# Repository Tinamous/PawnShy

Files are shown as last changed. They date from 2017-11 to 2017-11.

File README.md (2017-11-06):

# Pawn Shy

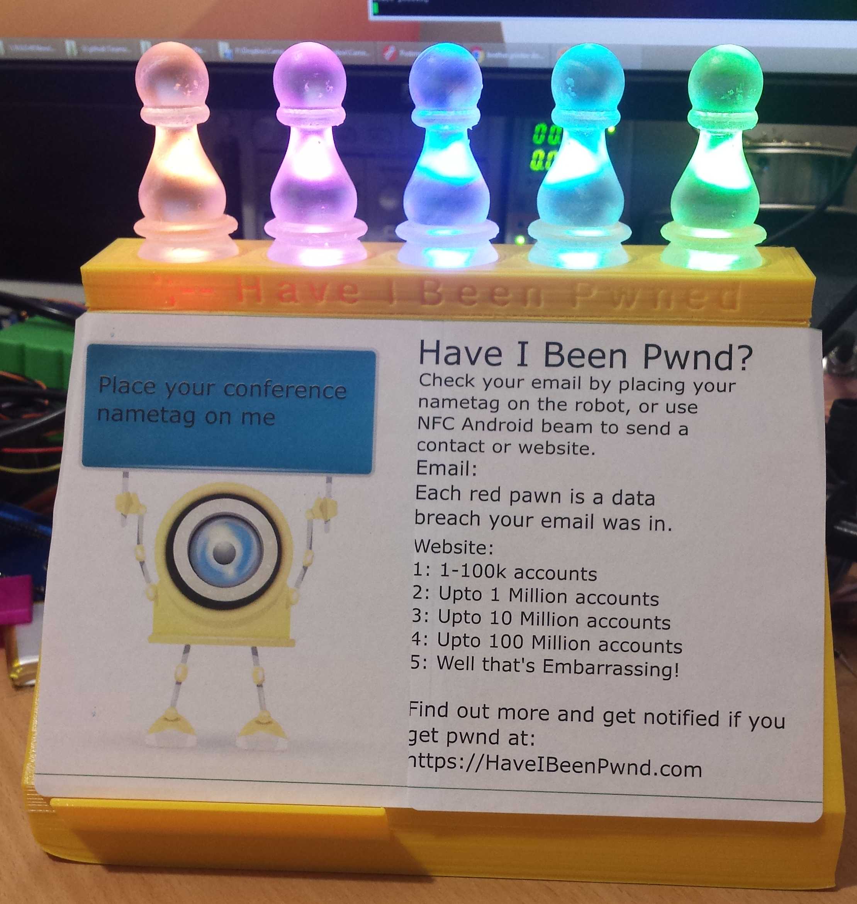
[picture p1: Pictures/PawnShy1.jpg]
Pawn Shy


This is my entry to the Have I Been Pwned API competition.

Based on the fair ground game Coconut shy. The aim is to knock out as many pawns as possible using either your email address or website that hasn't been pwned (good luck with that!).

## Videos:

[Part 1](https://youtu.be/ber4mi4SVx4)

[Part 2](https://youtu.be/kG7oJAG3vGs)

The game is intended to be easy to play, for example, at a conference, and to give the player a fun visual indication, and to drive their interest in Have I Been Pwned.

When attending Signal London recently I noticed the attendee name badges were actually NFC cards, this could be used either to lookup the attendees email (or hash) or have the email/hash directly in the NFC card.

Whilst the Signal NFC cards didn't actually include my email address it would have been easy for Twilio to add a VCard for me, or a hash of my email to facilitate this game.

Likewise, many door entry systems use NFC or RFID cards. These cards could be linked to an email address through an external database and provide a simple and fun way for employees to check if their email has been pwned.

## How It's Made

* Raspberry Pi running Raspbian
* I actually used the OctoPi 0.14 image for this. (It isn't required, but it makes it easy to start the Pi headless and I had other reasons as well)
* NFC sensor (Micro NFC Board - https://www.seeedstudio.com/Micro-NFC-Board-p-2431.html)
* 5 LED Neopixel strip (https://www.adafruit.com/product/1376)
* 3D Printed case
* 3D (SLA) printed pawns

The Raspberry Pi polls the NFC sensor waiting for a card or p2p connection and reads the following to get an email/website:

* Card serial number - linked though an external database to email address
* Uri NDEF record for a website
* VCard NDEF record for email address (Not implemented)
* P2P uri send for a website

Once the Pi picks up an email or website the Have I Been Pwned API is queried to get either:

* the number of times the email appears in a pwned site or 
* the number of accounts compromised for the website.

This is then displayed through the 5 pixel NeoPixel LEDs.

* As 0-5 Red/Purple vs Green/Yellow colouring for the count
* A sliding scale (1-100k, <1M, <10M, <100M, Wooo) of red/purple pwns indicting the number of accounts compromised.

Colours: typically Red for a compromise or Green when not used. However if using Minion pawns then Purple (bad minion) or Yellow (good minion/banana).

The LEDs are placed under the pawns and hidden from sight so it looks like the pawns are glowing.

Optional: A printer could be connected which prints out details of the compromise to allow the user to read up further.

## Games:

### Game 1: Have I Been Pwned

The aim of this game is to use your email address and make all the pawns go green (or yellow for Minion pawns).

Present a NFC card that either includes your email address, a hash or the id is linked to a database or email addresses (e.g. a door key)

Each red (or purple minion) pawn indicates the count of compromised sites the email is associated with.

### Game 2: Have They Been Pwned

The aim of this game is to find the website that has not been pwned, or in multi-player mode, to find the website with the lowest pwnage.

Using pre-programmed NFC cards, select a card for the website you trust the most. Present the the Game Of Pwned sensor.

Each red/purple pwnd indicates a pwnage.
0: Yay, not pwned!
1: 1-100k accounts compromised.
2: <1M
3: <10M
4: <100M
5: OUCH!

For multi-player you each select a card and the winner is the person with the lowest pwnage.

### Game 3: Send in the pwnage (Android Only)

Like game 2, the aim of this game is to find your favorite website without pwnage.

Ensure NFC Android Beam is enabled on your phone.

Browse to a website you trust (or don't!) and have an account with.

Place your phone on the Game Of Pwned.

When promoted by your phone click to send the website.

As with game 2. The pwnd accounts are displayed.

## Construction

### NeoPixels

Neopixels need to be driven with a serial data signal 70% of the power supply, and can work from a 3.6-5V Power supply. Sadly the Pi uses 3v3 for it's signals so the 3v3 power will not power the neopixels so our only choice is to use the 5V power. This then means that the 3v3 DIn will not be within the 70% required value. So we use a small diode inline with the 5V supply to drop it down to 4V4, brining our 3v3 signal to 75% of the power signal. With only 5 LEDs being driven the current draw should be low (300mA max) so a IN4001 diode will be more than sufficient.

* Cut a Neopixel strip to 5 LEDs along the cut line shown on the taps.
* Connect 3 wires to the input (5V/DIn/Gnd) side of the Neopixel strip.
* Connect a IN4001 diode in the 5V line with the current flow going towards the LEDs (diode band nearest the LEDs). Connect the other end of the diode to the 5V Pin.
* Connect a 300-600 Ohm resistor to the Din wire (to limit the current and protect the LEDs). Connect the other end of this to Pin 12 on the Pi).
* Connect Gnd straight to the Pi.

Note that Neopixels are not really a good choice for use on the Raspberry Pi. 

Install the raspberry Pi Neopixel software following the instructions here:

https://learn.adafruit.com/neopixels-on-raspberry-pi/software

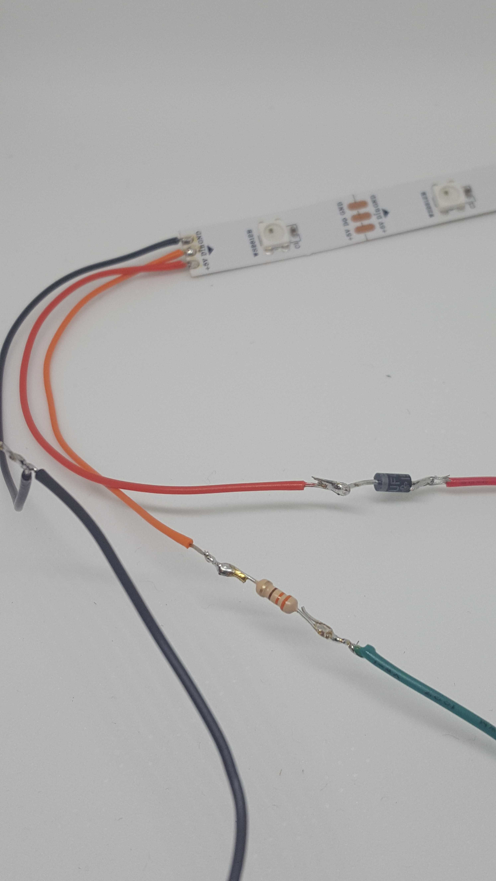
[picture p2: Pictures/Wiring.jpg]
Neopixel Wiring


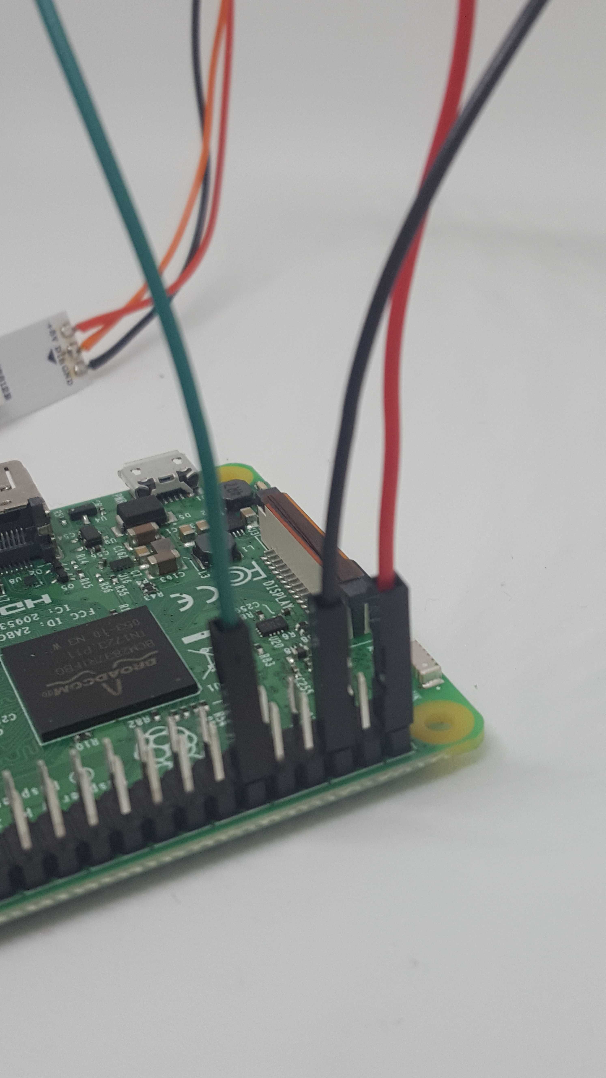
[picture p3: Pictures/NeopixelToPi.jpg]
Neopixel To Pi


## Pi

Ensure Neopixel LEDs connected as:

* Pin 2 = +5V
* Pin 6 = GND
* Pin 12 = DIn

Connect a USB power cable to the Pi before mounting (You might not be able to plug into the Pi once mounted).

Ensure your SD card in the Pi is working.

Mount the pi inside on the back wall. Use four M2.5 x6mm machine screws from the back into M2.5 x 11mm standoffs (Farnell 294583) which the Pi is mounted to, then M2.5 nuts on the other side of the Pi to secure it.

## NFC reader

If you're using M3 heat fit inserts to bold the holder to the case fit these with a hot soldering iron. Ensure that that are facing the correct way (fat end up with the large open area of the holder up as well).

Using a Micro NFC Board place this in the 3D printed holder with the component side of the PCB facing down into the holder so the blank side will sit against the inside of the case.

Fit the USB lead to the NFB board.

Screw the holder to the inside of the case. It doesn't quite fit in the center due to the USB connector, so it's pushed to one side.

Plug the USB lead into the Raspberry Pi.

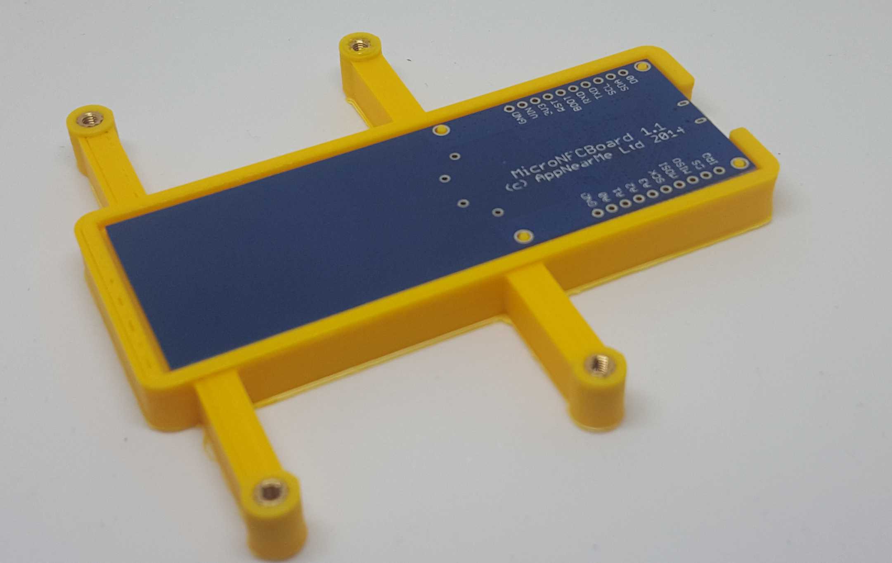
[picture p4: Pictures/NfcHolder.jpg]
NFC Holder


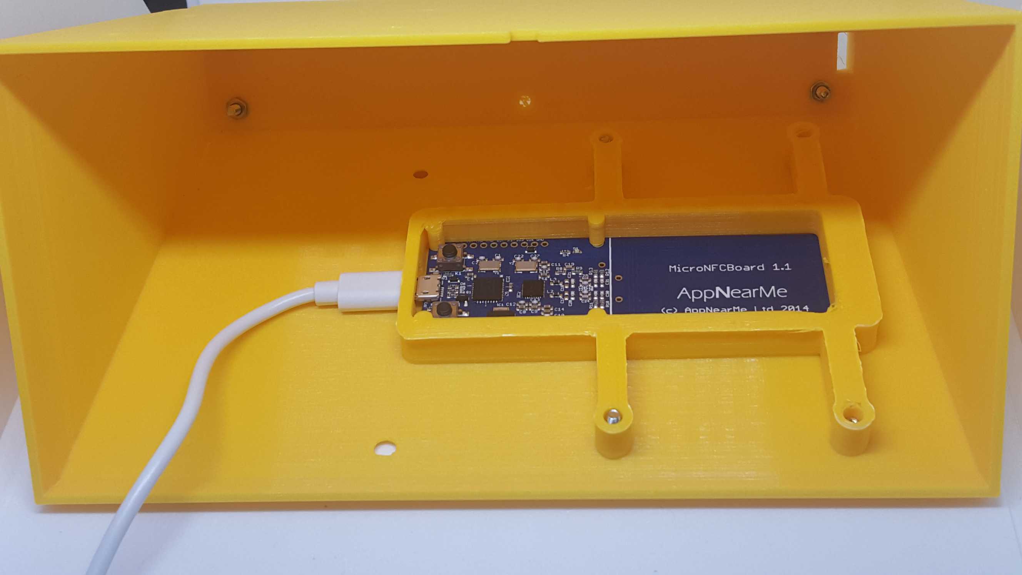
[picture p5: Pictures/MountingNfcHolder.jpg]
Mounting the NFC Holder


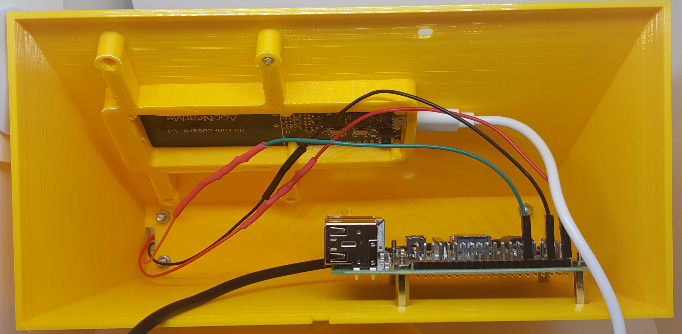
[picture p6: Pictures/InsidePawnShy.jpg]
Inside Pawn Shy


## Pawns:

The pawns are 3D Printed (I used a Form2 with clear resin as this gives a nice print). 

Various Pawn models are available:

* Eureka Pawn: https://www.thingiverse.com/thing:173436
* Bender Bust: https://www.thingiverse.com/thing:182789
* Bender Can Holder: http://www.thingiverse.com/thing:1513101
* Minions: https://www.thingiverse.com/thing:376059

The models should be resized to about 26mm on the x/y axis to fit the stand.

Eureka Pawn and Bender are also available in the Pawns folder as hollowed out versions which might work better for FDM printers with clear filament.

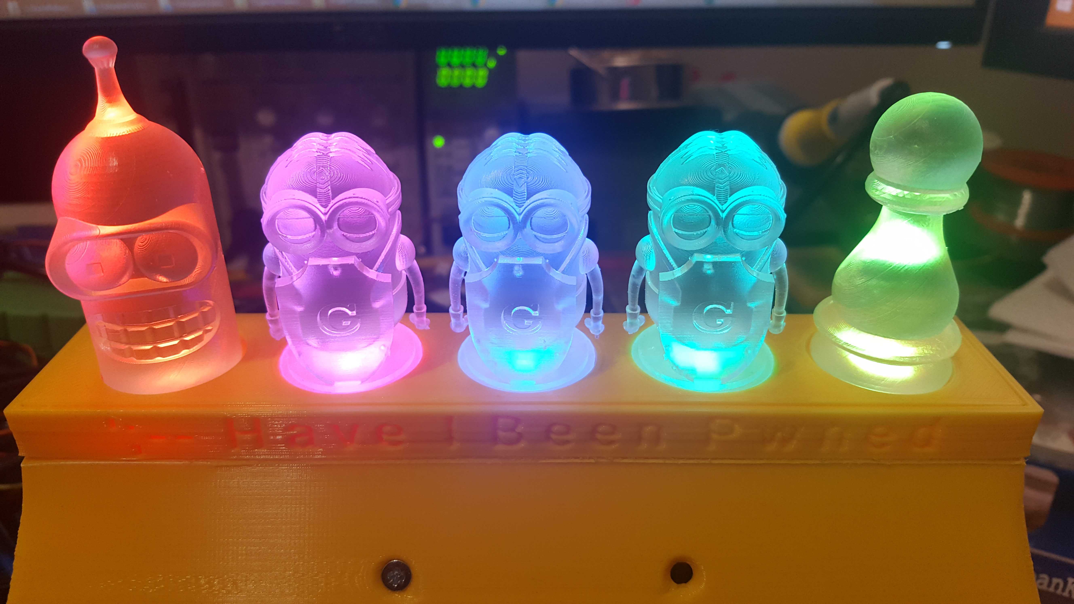
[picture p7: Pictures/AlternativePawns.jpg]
Alternative Pawns


### Printer Settings:

* Printer: Form2
* Resing: Clear (V2)
* Layer height: 0.1mm
* Placement: Manually placed to ensure supports are on the back/bottom.
* Supports: auto-generated

### Bluetooth printer notes:

Not implemented but a Bluetooth printer could be used to print out the pwned details.

https://www.cnet.com/uk/how-to/how-to-setup-bluetooth-on-a-raspberry-pi-3/

http://mattrichardson.com/Raspberry-Pi-Wireless-Photo-Printing/index.html

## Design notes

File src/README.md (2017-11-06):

# Pawn Shy Software

Written in Python 2.7.

Needs MicroNFCBoard, this is directly copied into the file structure from AppNearMe git repository.

Install the raspberry Pi Neopixel software following the instructions here:

https://learn.adafruit.com/neopixels-on-raspberry-pi/software

## Files

* app.py - the main application. run this using: $ sudo python app.py
* cardIdLookup.py - intended to do card serial number to email/domain. Unused at present
* hibpLookup.py - responsible for getting the count for pwned emails/accounts/domains from HaveIBeenPwned.com
* ledDriver.py - responsible for driving the LED (pawn) display
* nfcReader - interfaces to the NFC board to read tags or p2p connections.
* testers/MicroNFCBoardTest.py - this script connects to the MicroNFCBoard and watches for either a P2P connection or a tag
* testers/Neopixels.py - test for the Neopixel driver

## Run the application.

* clone this repository
* ensure you've set-up the NFC and NeoPixel libraries as described in the main readme
* open the .src folder
* use 
** sudo python app.py

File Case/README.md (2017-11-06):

# Case

## Contents

The case consists of the following parts.

* MainBody - This is the large body containing the Rasberry Pi, NFC reader.
* LEDHolder - This bolts on opt of the main body (use M3 counter sunk machine screws).
* PawnStand - Sits on inside the LED holder, has 26mm pockets to hold the pawns.

Inside the main body the NFC sensor is attached to the front panel by 4x M3 countersunk machine screws. You can use either heatfit inserts into the holder or long bolts (15+mm) and nuts.

The Raspberry Pi is attached inside the back panel with standoffs. It is expected the power cable goes up from the Pi inside the case and then down and out through the hole in the back (or to an internal battery).

The sensor holder has mointing points well outside the main body area to allow for different RFID/NFC sensors that might be large.

Two sensor holders are provided:

* MicroNFCBoardCase - This is for the MicroNFCBoard (https://www.seeedstudio.com/Micro-NFC-Board-p-2431.html)
* UniversalRfidCase - For IB Technology (Eccel) Micro RWD Universal PCB (http://www.ibtechnology.co.uk/rfid-readers/)

Optional base:

* Base - Holds a USB battery pack, allows for stick feet and a stand for a phone to help align with the NFC sensor.

## Printing

All parts can be printed on a FDM 3D Printer. 

My settings:

* Printer: Ultimaker 2 Extended+
* Nozzle: 0.6mm (0.4 should be fine, I used 0.6 as my 0.4 is trashed and 0.6 is faster).
* Adhesion: Brim (Optional)
* Layer Height: 0.2mm
* Wall thickness: 1.59mm
* Top/Bottom thickness: 1.2mm
* Infill Density: 20%
* Supports: No (Ensure models are flipped as needed).

None of these settings are critical.

Most parts will need rotating 180° to ensure the flat side is against the bed.

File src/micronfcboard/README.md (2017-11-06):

# Micro NFC Board Python API.

From: https://github.com/AppNearMe/micronfcboard-python

Direct copy as not available through pip

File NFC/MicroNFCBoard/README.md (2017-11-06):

# Using the Micro NFC Board Reader

Update firmware following instructions from: https://github.com/AppNearMe/micronfcboard-python

(Note: I used windows, the USB bulk storage worked nicely).

Install Libusb: https://askubuntu.com/questions/629619/how-to-install-libusb

$ sudo apt-get install libusb-1.0-0-dev

$ sudo apt-get install libusb-1.0-21-dev

Pi might already have this installed.

$ ldconfig -p | grep libusb 

https://github.com/walac/pyusb

(Starting with OctoPi 0.14)

Install Pip:
sudo apt-get install python-pip

Install PyUSB:

$ sudo pip install pyusb

// Get the examples.
git clone https://github.com/AppNearMe/micronfcboard-python.git

run blink example to check for working connection to the board.

needed to be run as sudo.

$ sudo python blink.py

------------------
To access the USB device without needing sudo we add a udev rule for the device:

Nfc board USB Id: 1fc9:8039

Create the rules file:

sudo nano /etc/udev/rules.d/99-local.rules

Add:

SUBSYSTEM=="usb", ATTRS{idVendor}=="1fc9", MODE="0666"

Reload (remove USB device as well):

$ udevadm control --reload-rules

------------------

You can then use:

$ python blink.py

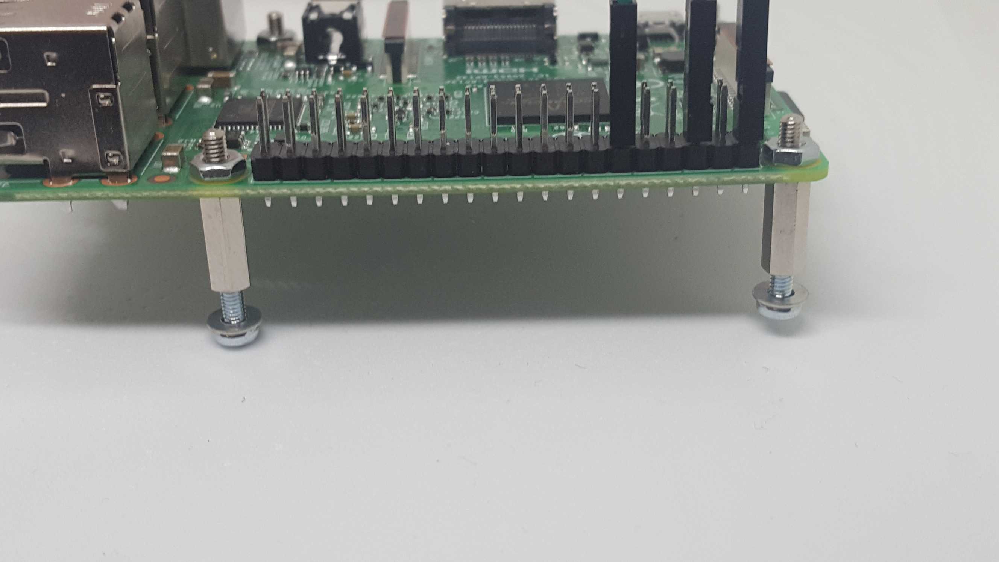
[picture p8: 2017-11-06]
Pictures/PiStandoffs.jpg

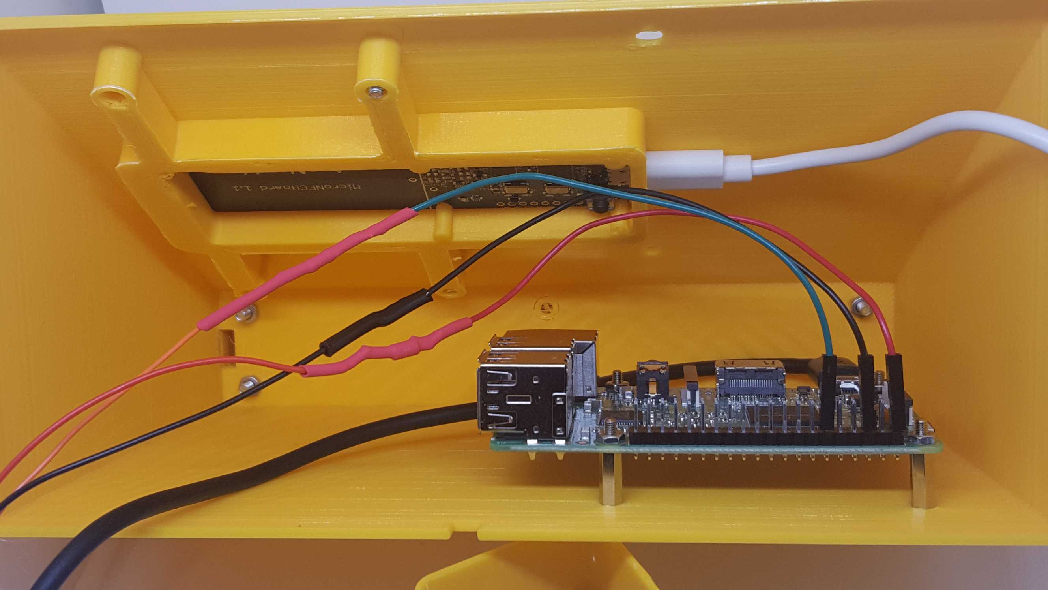
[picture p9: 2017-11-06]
Pictures/PiAndNfcMount.jpg

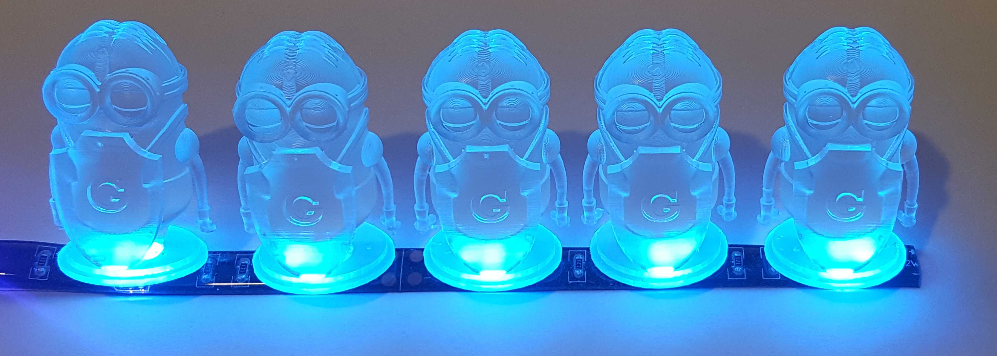
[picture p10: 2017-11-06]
Pictures/MinionsInUvLight.jpg

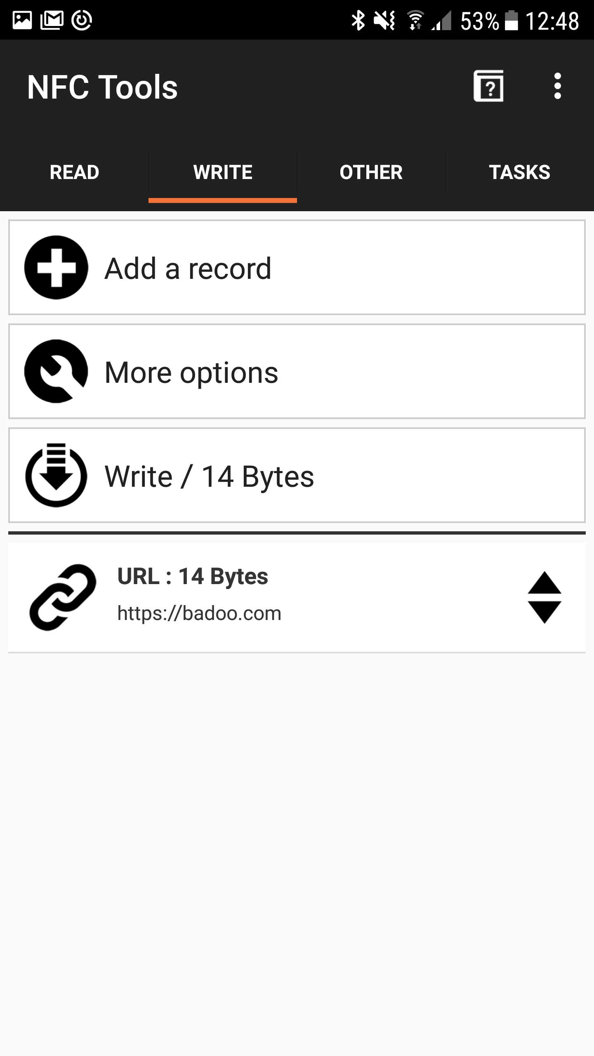
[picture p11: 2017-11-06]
Pictures/WritingTag-2.jpg

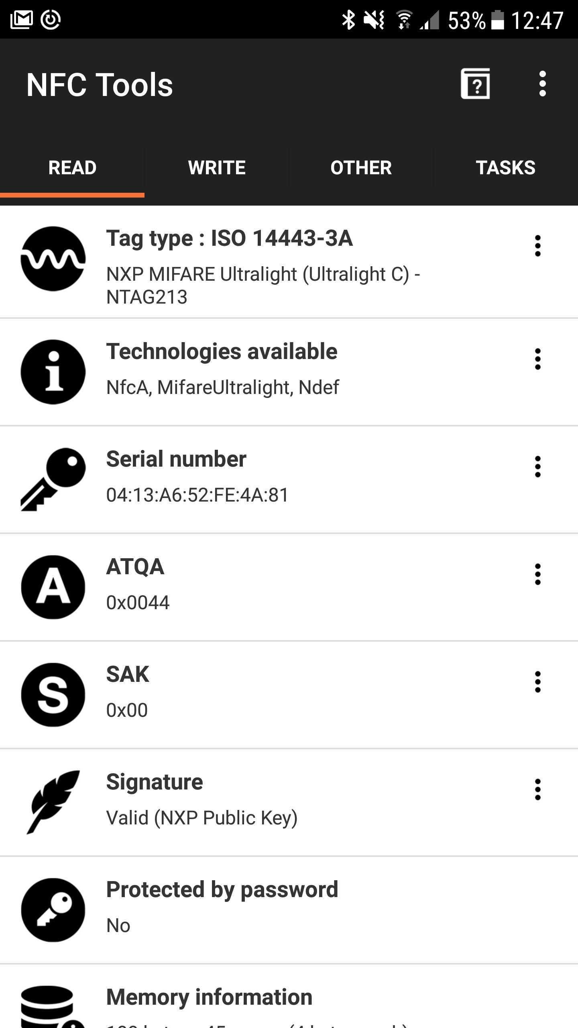
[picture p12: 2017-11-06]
Pictures/WritingTag-1.jpg

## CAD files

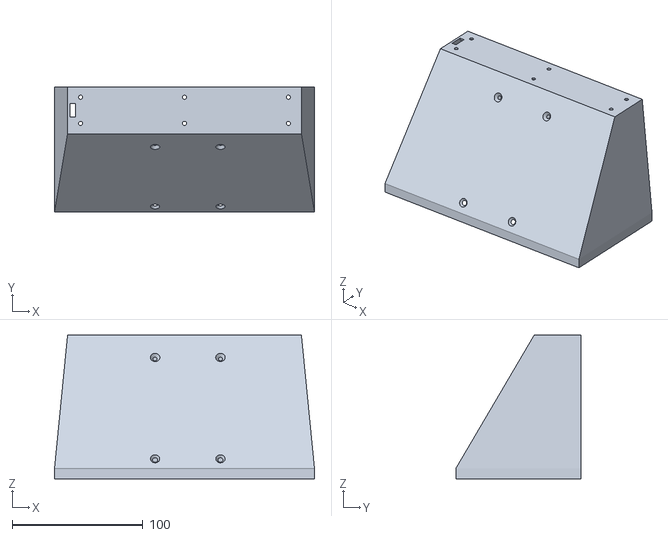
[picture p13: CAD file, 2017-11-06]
Case/MainBody.stl
199.0 x 96.0 x 110.1

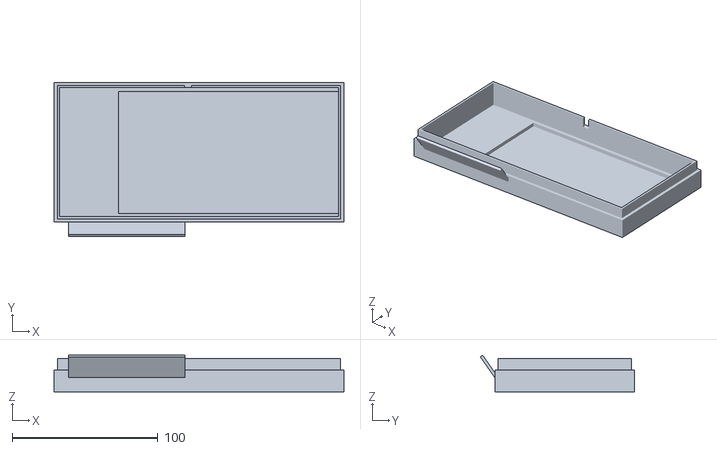
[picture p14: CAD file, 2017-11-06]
Case/Base.stl
199.0 x 106.0 x 25.1

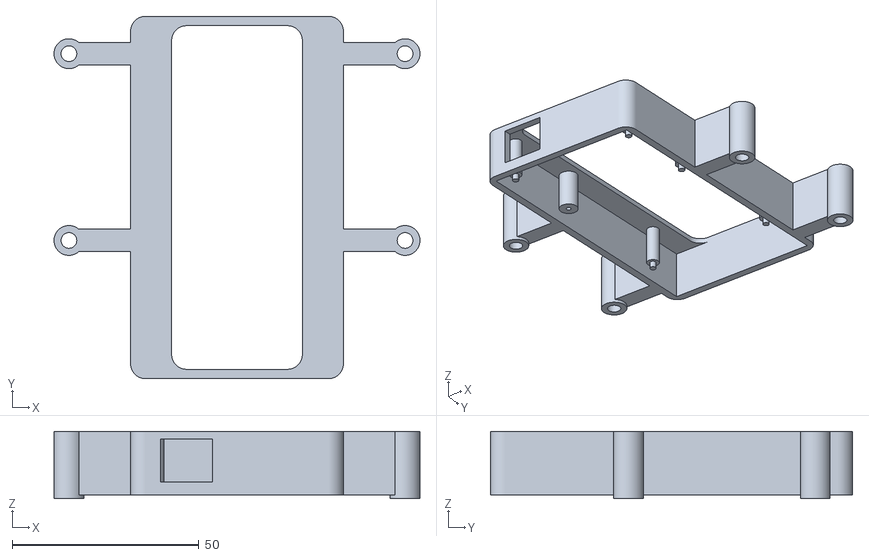
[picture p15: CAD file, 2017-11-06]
Case/UniversalRfidCase.stl
98.0 x 97.0 x 18.0

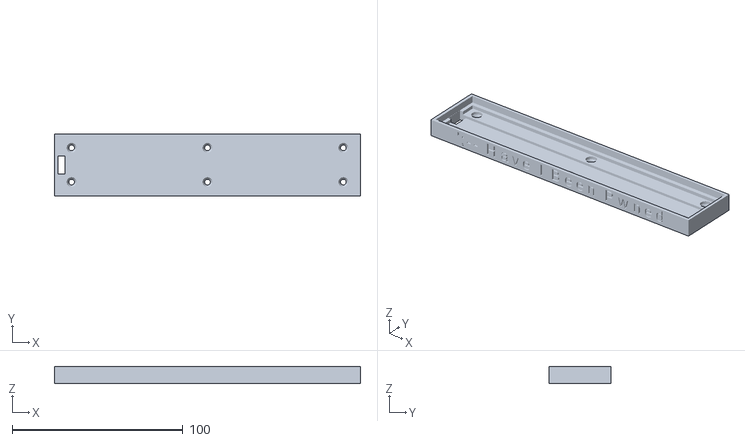
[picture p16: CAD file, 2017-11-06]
Case/LEDHolder.stl
179.0 x 36.0 x 10.0

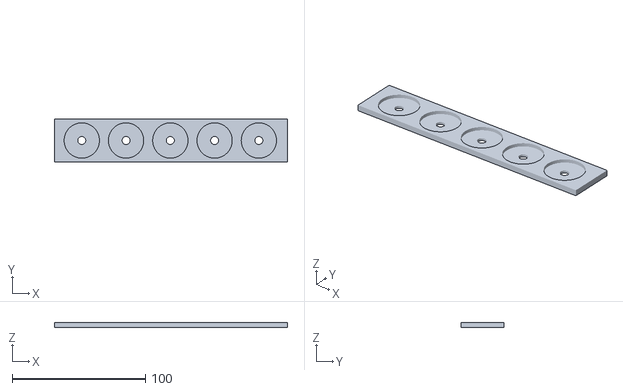
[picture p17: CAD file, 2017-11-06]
Case/PawnStand.stl
175.0 x 32.0 x 4.00

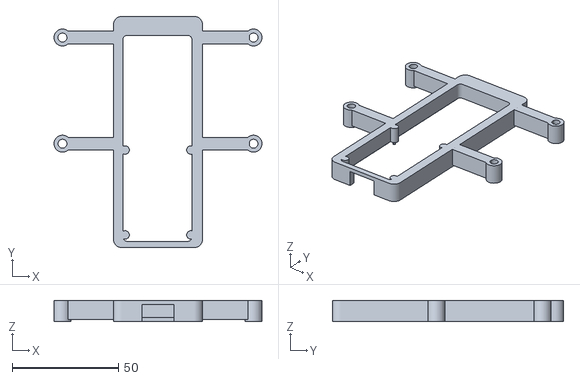
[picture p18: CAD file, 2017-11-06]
Case/MicroNFCBoardCase.stl
98.0 x 109.0 x 10.0

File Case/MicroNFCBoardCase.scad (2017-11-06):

$fn=60;
curveRadius = 4;
wallWidth = 3;

totalWidth = 36 + 2*wallWidth;
totalHeight = 103+ + 2*wallWidth;

// NB: Uses M2 Screws.

// If the case is an insert for the badger/dymo case
//caseMountingStyle = 0; // Ultimaker Lid
//caseMountingStyle = 1; // Badger
caseMountingStyle = 2; // Have I Been Pwned (main case has holes closer - I measured wrong!)
//caseMountingStyle = 3; // Alternative UM lid for NCF PCB

module rfidReaderHoleChecker() {
    // PCB + underneath aerial.
    cube([35.2,100,1.6]);
    // Making points where the holes are expected to go to test 
    // alignment with actual PCB
    holeHeight = 3;
    holeDiameter = 1.2;

    // PCB holes
    // LHS
    translate([2,0,0]) {
        translate([0,2.5,0]) {
            cylinder(d=holeDiameter, h=holeHeight);
        }
        translate([0,42.5,0]) {
            cylinder(d=holeDiameter, h=holeHeight);
        }
        
    }
    
    // RHS
    translate([33,0,0]) {
        translate([0,2.5,0]) {
            cylinder(d=holeDiameter, h=holeHeight);
        }
        
        translate([0,42.5,0]) {
            cylinder(d=holeDiameter, h=holeHeight);
        }
    }
}

module rfidReader() {
    
    //cube([51,91,16]);
    holeDiameter = 3;
    difference() {
        union() {
            // PCB + underneath aerial.
            cube([35.2,100.2,1.6]);
            // USB socket
            translate([13.5,0,0]) {
                // Buttons are 7mm, USB socked is lower
                // but show it as 7mm to save modelling the buttons also.
                cube([7,5,7]);
            }
            
            // USB Plug
            translate([10.5,-25,-1]) {
                cube([12,25,7]);
            }
            
            
            // Buttons
            translate([8,6,0]) {
                cylinder(d=4, h=5);
            }
            translate([27.5,6,0]) {
                cylinder(d=4, h=5);
            }

            // LEDs
            translate([5,37,0]) {
                cylinder(d=1, h=15);
            }
            translate([31,37,0]) {
                cylinder(d=1, h=15);
            }
        }
        union() {
            // PCB holes
            // LHS
            translate([2,0,0]) {
                translate([0,2.5,0]) {
                    #cylinder(d=holeDiameter, h=20);
                }
                translate([0,42.5,0]) {
                    #cylinder(d=holeDiameter, h=20);
                }
            }
            
            // RHS
            translate([33,0,0]) {
                translate([0,2.5,0]) {
                    #cylinder(d=holeDiameter, h=20);
                }
                translate([0,42.5,0]) {
                    #cylinder(d=holeDiameter, h=20);
                }
            }
        }
    }
}

module GenericBase(xDistance, yDistance, zHeight, zAdjust) {
	    
    // NB: base drops below 0 line by the curve radius so we need to compensate for that
	translate([curveRadius,curveRadius, zAdjust]) {
		minkowski()
		{
			// 3D Minkowski sum all dimensions will be the sum of the two object's dimensions
			cube([xDistance-(curveRadius*2), yDistance-(curveRadius*2), (zHeight /2)]);
			cylinder(r=curveRadius,h= (zHeight/2) + curveRadius);
		}
	}
}

module genericBase2(width, height, depth, cornerDiameter) {
//cornerDiameter = 5;
cornerRadius = cornerDiameter/2;

    translate([cornerDiameter/2,0,0]) {
        cube([width-cornerDiameter, height, depth]);
    }
    
    translate([0,cornerDiameter/2,0]) {
        cube([width, height-cornerDiameter, depth]);
    }
    
    translate([cornerRadius,cornerRadius,0]) {
        cylinder(d=cornerDiameter, h=depth);
    }
    
    translate([width-cornerRadius,cornerRadius,0]) {
        cylinder(d=cornerDiameter, h=depth);
    }
    
    translate([cornerRadius,height-cornerRadius,0]) {
        cylinder(d=cornerDiameter, h=depth);
    }
    
    translate([width-cornerRadius,height-cornerRadius,0]) {
        cylinder(d=cornerDiameter, h=depth);
    }
}

pcbDepth = 2;

module caseOuter() {
holeHeight = 8;
holeSupportDiameter = 6;
holeInnerDiameter = 3.2;
    
    difference() {
        union() {
            //PCB 51,91,16
            //GenericBase(51 + 2*wallWidth, 91+ 2*wallWidth, 16-5+2 + 0.5, 0);
            genericBase2(totalWidth, totalHeight, 10, 8);
        }
        union() {
            // Inner cutout
            translate([wallWidth+1.5, wallWidth, -0.01]) {
                // PCB: 35x100
                // take to 103.
                // but... not here.
                genericBase2(32.5,97,11,4);
                //cube([33, 99, 9]);
            }
            
            // Hollow out PCB
            translate([wallWidth-0.5, wallWidth, 0]) {
                    // Hollow out the same but longer for the PCB
                    // so leaving a ridge for the end of the PCB to sit on
                    // hopefully at the same height as the pcb mounts!
                    cube([37, 102.5, pcbDepth]);               
            }
            
            // Cut through the base for the the badger
            // case to reduce print time, allow ventilation
            // and view the LEDs on the PCB.
            if (caseMountingStyle==1 || caseMountingStyle==2) {
                translate([wallWidth+4.5, wallWidth, -0.1]) {
                    genericBase2(36-10, 97, 11, 8);
                }
            }
            
            // USB input
            translate([11 + (wallWidth + 0.5) - 1,-5,-0.01]) {
                cube([15,10,8]);
            }
        }
    }
    
    
    // Screw posts for the NFC PCB.
    translate([wallWidth+0.5, wallWidth+0.5,pcbDepth]) {                
        mountingPin(2,2.5);
        mountingPin(2,42.5);
    
        mountingPin(33,2.5);
        mountingPin(33,42.5);
    }
    
    
}

// Mouting pin for the FRID reader.
module mountingPin(x,y) {
holeHeight = 10;
holeSupportDiameter = 6;
    
    translate([x,y,0]) {
        cylinder(d=4, h=holeHeight-pcbDepth);
        translate([0,0,-2]) {
            // PCB holes are 1.8mm
            // pin isn't so critical as PCB will be sandwiched between case and enclosure.
            cylinder(d=1.2, h=holeHeight-pcbDepth);
        }
    }
}

// Mounting hole for the RFID reader
module mountingHole(x,y) {
holeHeight = 13.5;
holeSupportDiameter = 6;
holeInnerDiameter = 1.6;
    translate([x,y,0]) {
        difference() {
            union() {
                cylinder(d=holeSupportDiameter, h=holeHeight);
            }
            union() {
                cylinder(d=holeInnerDiameter, h=holeHeight-5);
            }
        }
    }
}

// Mounting hole for the case.
module caseMountingHole(x,y, height, holeSize) {

    translate([x,y,0]) {
        difference() {
            union() {
                cylinder(d=8, h=height);
            }
            union() {
                translate([0,0,-0.01]) {
                    cylinder(d=holeSize, h=height + 0.02);
                }
            }
        }
    }
}

// Top/Bottom (length) of case
module caseMounts(height, holeSize) {
    caseMountingHole(totalWidth/2, totalHeight + 2, height, holeSize);
    caseMountingHole(totalWidth/2, - 2, , height, holeSize);
}

module caseMountConnector(x,y,height) {
    // -3 to allow for hole size and width of cube.
zOffset = 1;
    translate([x, y-3, zOffset ]) {
        cube([22, 6, height-zOffset ]);
    }
}

// Sides to to fit the badger label printer case.
module badgerCaseMounts(height, holeSize) {
    
    echo("totalWidth:", totalWidth);
    
midXHoles = 90/2; // 45
midCase = totalWidth/2; // 57/2 = 28.5
offset = midXHoles - midCase;
//offset2 - midXHoles - 

// 10mm offset for first    
firstMountY = totalHeight - 10;
yDistanceBetweenMounts = 55;
    
    echo("offset:", offset);

    // Raise the mouting points up 1mm
    translate([0,0,-0.01]) {
        // 90mm between 8 axis mounts
        // Top 2 (furthest from USB
        caseMountingHole(midCase + midXHoles, firstMountY, height, holeSize);
        caseMountConnector(totalWidth, firstMountY, height);
        
        caseMountingHole(midCase - midXHoles, firstMountY, height, holeSize);
        caseMountConnector(midCase - midXHoles+2.5, firstMountY, height);
        
        // 55mm gap on y axis
        caseMountingHole(midCase + midXHoles, firstMountY-yDistanceBetweenMounts, height, holeSize);
        caseMountConnector(totalWidth, firstMountY-yDistanceBetweenMounts, height);
        
        caseMountingHole(midCase - midXHoles, firstMountY-yDistanceBetweenMounts, height, holeSize);
        caseMountConnector(midCase - midXHoles+2.5, firstMountY-yDistanceBetweenMounts, height);
    }
}

module haveIBeenPwnedCaseMounts(height, holeSize) {
         
midXHoles = 90/2; // 45
midCase = totalWidth/2; // 57/2 = 28.5
offset = midXHoles - midCase;
//offset2 - midXHoles - 

// 10mm offset for first    
firstMountY = totalHeight - 10;
yDistanceBetweenMounts = 50;
    
    echo("offset:", offset);
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

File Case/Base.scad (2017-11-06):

module showMainBody() {
    import("MainBody.stl");
}


difference() {
    union() {   
        cube([199, 96, 15]);

        translate([2.25, 2.25,0]) {
            cube([199-4.5, 96-4.5, 23]);
        }
        
        // Add a support for a phone.
        
        //translate([(199-80)/2,-10,24]) { - center - NFC reader issues.
        translate([10,-10,24]) {
            rotate([-55, 0, 0]) {
                cube([80, 20, 2]);
            }
        }
    }
    union() {
        
        // Main body cutout, but only down to 
        // 4mm to allow for a little pocket for the battery
        translate([3.75, 3.75,4]) {
            cube([199-7.5, 96-7.5, 25]);
        }
        
        // Battery cutout.
        translate([199-149-5.75, 6,1]) {
            #cube([151, 83.5, 25]);
        }
        
        // back cable cutout.
                // Power cable for the Pi.
        translate([179/2, 90, 15]) {
            #cube([5,15,15]);
        }
    }
}


translate([0,0,25]) {
    %showMainBody();
}

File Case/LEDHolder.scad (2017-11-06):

module minionStandModel() {
    cube([175, 32, 4]);
}

module ledTapeModel() {
    // TODO: Allow for connecting wires!
    color("red") {
        cube([166, 10, 0.5]);
        for (ledNumber = [0 : 4]) {
            translate([(33.5 * ledNumber) + 16.9+2.5,2.5,0]) {
                cube([5,5,2]);
            }
        }
    }
}



module showModels() {
    translate([2,2,4]) {
        translate([3.8,11,0]) {
            //%ledTapeModel();
        }

        translate([0, 0, 2]) {
            //%minionStandModel();
        }
    }
}

showModels();

height = 10;

difference() {
    union() {
        cube([175+4,32+4, height]);
        
    }
    union() {
        addText();
        
        translate([1.9,1.9,height-4]) {
            // Hollow out the inside for the top 
            // minion stand.
            cube([175.5,32.5, 4.01]) ;
        }
        
        // Hollow out down to the level of nearly full hegith
        // for the leds.
        translate([4,4, height - (4+2)]) {
            cube([175-4,32-4, 2.01]) ;
        }
        
        // Cutout for LEDs
        // 2,2 offset for case outer.
        // 20.5mm to first minion (i.e. first LED).
        // 33.5mm spacing between LEDS.
        // so 33.5/2 (16.7mm) from the tape start
        // to the first LED.
        // 20.5 - 16.7 = 3.8mm offset for the tape start.
        // +0.5 on the depth to allow for a little fudge factor
        // when it's all mounted.
        translate([2 + 3.8, 2 + ((32-10.5)/2), height - (4+2+1.5)]) {
            cube([170,10.5, 2.11]) ;
        }
        
        // Cut out for LED connecting wires.
        translate([2, 2 + ((32-10.5)/2), -0.01]) {
            cube([4,10.5, height + 0.1]) ;
        }
        
        // Mounting holes.
        mountingHoles();
       
    }
}

$fn=80;

module mountingHoles() {
    translate([10, 8, -0.1]) {
        mountingHole();
    }
    
    translate([10, 36-8, -0.1]) {
        mountingHole();
    }
    
    translate([179/2, 8, -0.1]) {
        mountingHole();
    }
    
    translate([179/2, 36-8, -0.1]) {
        mountingHole();
    }
    
    translate([179-10, 8, -0.1]) {
        mountingHole();
    }
    
    translate([179-10, 36-8, -0.1]) {
        mountingHole();
    }
}

module mountingHole() {
    
    cylinder(d1=3.2, d2=6.2, h=3);
    
    translate([0,0,2.5]) {
        cylinder(d=6.2, h=3);
    }
}

module addText() {
    translate([18,1.2,2]) {
        rotate([90,0,0]) {
            linear_extrude(1.5) {
                #text("';-- Have I Been Pwned", 7, spacing=1.5);
            }
        }
    }
}

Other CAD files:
Case/MainBody.scad
Case/PawnStand.scad
Case/UniversalRfidCase.scad

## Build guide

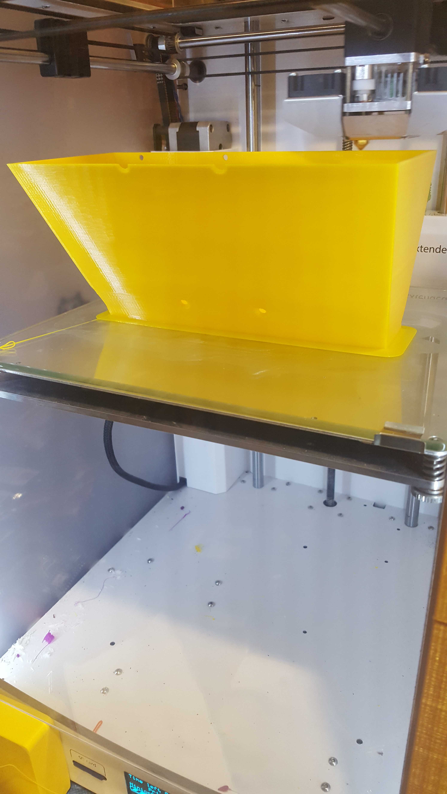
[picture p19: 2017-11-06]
Pictures/PrintingTheCase.jpg

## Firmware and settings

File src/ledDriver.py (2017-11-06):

# Mainly copied from NeoPixel strandtest example. Author: Tony DiCola (tony@tonydicola.com)
# See: https://github.com/jgarff/rpi_ws281x

import threading
import time

from neopixel import *

# Led Driver for Pawn Shy to animate / set the Pawn LED states.
class LedDriver():

	def __init__(self):
		# LED strip configuration:
		LED_COUNT      = 5      # Number of LED pixels.
		LED_PIN        = 18      # GPIO pin connected to the pixels (18 uses PWM!).
		LED_FREQ_HZ    = 800000  # LED signal frequency in hertz (usually 800khz)
		LED_DMA        = 5       # DMA channel to use for generating signal (try 5)
		LED_BRIGHTNESS = 255     # Set to 0 for darkest and 255 for brightest
		LED_INVERT     = False   # True to invert the signal (when using NPN transistor level shift)
		LED_CHANNEL    = 0       # set to '1' for GPIOs 13, 19, 41, 45 or 53
		LED_STRIP      = ws.WS2811_STRIP_GRB   # Strip type and colour ordering

		# Create NeoPixel object with appropriate configuration.
		self.strip = Adafruit_NeoPixel(LED_COUNT, LED_PIN, LED_FREQ_HZ, LED_DMA, LED_INVERT, LED_BRIGHTNESS, LED_CHANNEL, LED_STRIP)

		#self.bad_color = Color(255, 0, 0)
		self.bad_color = Color(128, 0, 128) # Purple
		#self.good_color = Color(0, 0, 0) # Off
		self.good_color = Color(255, 255, 0) # Minion Yellow

		# Intialize the library (must be called once before other functions).
		self.strip.begin()

		# Idle
		self.display_mode = 0
		self.pwn_count = 0
		self.running = False
		self.counter = 0
		self.result_shown = False

	# Animate the LEDs whilst we wait for a user input
	def animate_whilst_not_busy(self):
		self.counter = 0
		self.display_mode = 0

	# Animate the LEDs whilst the HIBP result is being retreived
	def animate_whilst_hibp_lookup(self):
		self.counter = 0
		self.display_mode = 1

	# show the result from an email lookup. count should be the
	# number of times the email address was pwned
	def show_result_email_count(self, count):
		self.counter = 0
		self.display_mode = 2
		self.pwn_count = count
		self.result_shown = False

	# show the results from a domain lookup. count should be the number
	# of accounts compromised
	def show_result_web_count(self, count):
		self.counter = 0
		self.display_mode = 3
		self.pwn_count = count
		self.result_shown = False

	# Start a background thread to show the status
	def start(self):
		self.display_mode = 0
		self.running = True

		# start a thread to run the LED animations in the background.
		thread = threading.Thread(target=self.run_animations, args=())
		thread.daemon = True  # Daemonize thread
		thread.start()

	def stop(self):
		self.running = False

	# Thred target to show status.
	def run_animations(self):

		while self.running:
			self.counter = self.counter + 1;

			if self.display_mode == 0:
				self._show_idle()
			elif self.display_mode == 1:
				self._show_hibp_lookup()
			elif self.display_mode == 2:
				self._show_email_result()
			elif self.display_mode == 3:
				self._show_web_result()

	def _show_idle(self):
		#self.theaterChaseRainbow(self.strip, 20, 1)

		for i in range(self.strip.numPixels()):
			self.strip.setPixelColor(i, self.wheel((int(i * 256 / self.strip.numPixels()) + self.counter) & 255))

		self.strip.show()
		time.sleep(20 / 1000.0)

		if self.counter > 255:
			self.counter = 0

	def _show_hibp_lookup(self):
		#self.rainbowCycle(self.strip, 2, 1)

		"""Draw rainbow that uniformly distributes itself across all pixels."""
		for i in range(self.strip.numPixels()):
			self.strip.setPixelColor(i, self.wheel((int(i * 256 / self.strip.numPixels()) +  self.counter) & 255))
		self.strip.show()
		time.sleep(2 / 1000.0)

		if self.counter > 255:
			self.counter = 0

	def _show_email_result(self):
		if self.result_shown:
			time.sleep(0.01)
			return;

		# Count 5+ all leds.
		# Count 4, LED1 Off
		# Count 3, LED1,2 Off
		# Count 2, LED1,2,3 Off
		# Count 1, LED1,2,3,4 Off
		# Count 0, LED1,2,3,4,5 Off

		for i in range(self.strip.numPixels()):
			self.strip.setPixelColor(i, self.good_color)
		self.strip.show()

		self.animate_results(self.strip, 0)
		self.strip.setPixelColor(0, self.bad_color if self.pwn_count>=5 else self.good_color)

		if self.pwn_count < 5:
			self.animate_results(self.strip, 1)
		self.strip.setPixelColor(1, self.bad_color if self.pwn_count>=4 else self.good_color)

		if self.pwn_count < 4:
			self.animate_results(self.strip, 2)
		self.strip.setPixelColor(2, self.bad_color if self.pwn_count>=3 else self.good_color)

		if self.pwn_count < 3:
			self.animate_results(self.strip, 3)
		self.strip.setPixelColor(3, self.bad_color if self.pwn_count>=2 else self.good_color)

		if self.pwn_count < 2:
			self.animate_results(self.strip, 4)
		self.strip.setPixelColor(4, self.bad_color if self.pwn_count>=1 else self.good_color)

		self.strip.show()
		self.result_shown = True

	def _show_web_result(self):
		if self.result_shown:
			time.sleep(0.01)
			return;

		for i in range(self.strip.numPixels()):
			self.strip.setPixelColor(i, self.good_color)

		self.animate_results(self.strip, 0)
		self.strip.setPixelColor(0, self.good_color if self.pwn_count < 100000000 else self.bad_color)

		if self.pwn_count < 100000000:
			self.animate_results(self.strip, 1)
		self.strip.setPixelColor(1, self.good_color if self.pwn_count < 10000000 else self.bad_color)

		if self.pwn_count < 10000000:
			self.animate_results(self.strip, 2)
		self.strip.setPixelColor(2, self.good_color if self.pwn_count < 1000000 else self.bad_color)

		if self.pwn_count < 1000000:
			self.animate_results(self.strip, 3)
		self.strip.setPixelColor(3, self.good_color if self.pwn_count < 100000 else self.bad_color)

		if self.pwn_count < 100000:
			self.animate_results(self.strip, 4)
		self.strip.setPixelColor(4, self.good_color if self.pwn_count < 1 else self.bad_color)

		self.strip.show()
		self.result_shown = True

	def animate_results(self, strip, start, wait_ms=1, iterations=10):
		# Animate pawns starting at start
		# so giving a count down.
		for j in range(0, 256 * iterations, 2):
			for i in range(start, strip.numPixels()):
				strip.setPixelColor(i, self.wheel((int(i * 256 / strip.numPixels()) + j) & 255))
			strip.show()
			time.sleep(wait_ms / 1000.0)

	# Define functions which animate LEDs in various ways.
	def colorWipe(self, strip, color, wait_ms=50):
		"""Wipe color across display a pixel at a time."""
		for i in range(strip.numPixels()):
			strip.setPixelColor(i, color)
			strip.show()
			time.sleep(wait_ms / 1000.0)

	def theaterChase(self, strip, color, wait_ms=50, iterations=10):
		"""Movie theater light style chaser animation."""
		for j in range(iterations):
			for q in range(3):
				for i in range(0, strip.numPixels(), 3):
					strip.setPixelColor(i + q, color)
				strip.show()
				time.sleep(wait_ms / 1000.0)
				for i in range(0, strip.numPixels(), 3):
					strip.setPixelColor(i + q, 0)

	def wheel(self, pos):
		"""Generate rainbow colors across 0-255 positions."""
		if pos < 85:
			return Color(pos * 3, 255 - pos * 3, 0)
		elif pos < 170:
			pos -= 85
			return Color(255 - pos * 3, 0, pos * 3)
		else:
			pos -= 170
			return Color(0, pos * 3, 255 - pos * 3)

	def rainbow(self, strip, wait_ms=20, iterations=1):
		"""Draw rainbow that fades across all pixels at once."""
		for j in range(256 * iterations):
			for i in range(strip.numPixels()):
				strip.setPixelColor(i, self.wheel((i + j) & 255))
			strip.show()
			time.sleep(wait_ms / 1000.0)

	def rainbowCycle(self, strip, wait_ms=20, iterations=5):
		"""Draw rainbow that uniformly distributes itself across all pixels."""
		for j in range(256 * iterations):
			for i in range(strip.numPixels()):
				strip.setPixelColor(i, self.wheel((int(i * 256 / strip.numPixels()) + j) & 255))
			strip.show()
			time.sleep(wait_ms / 1000.0)

	def theaterChaseRainbow(self, strip, wait_ms=50):
		"""Rainbow movie theater light style chaser animation."""
		for j in range(256):
			for q in range(3):
				for i in range(0, strip.numPixels(), 3):
					strip.setPixelColor(i + q, self.wheel((i + j) % 255))
				strip.show()
				time.sleep(wait_ms / 1000.0)
				for i in range(0, strip.numPixels(), 3):
					strip.setPixelColor(i + q, 0)

# Main program logic follows:
if __name__ == '__main__':
	driver = LedDriver()

	print("Not busy animation")
	driver.animate_whilst_not_busy()
	driver.start()

	time.sleep(10.0)

	print("HIBP Lookup animation")
	driver.animate_whilst_hibp_lookup()
	time.sleep(10.0)

	print("Email count result")
	driver.show_result_email_count(2)
	time.sleep(20.0)

	print("Web result")
	driver.show_result_web_count(23567)
	#time.sleep(10.0)

	print("That's it, I'm out of here....")
	driver.stop()

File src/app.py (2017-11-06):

from hibpLookup import HibpLookup
from ledDriver import LedDriver
from nfcReader import NfcReader
from cardIdLookup import CardIdLookup

import time
from micronfcboard.board import MicroNFCBoard
from micronfcboard.nfc.ndef import URIRecord, TextRecord, SmartPosterRecord, MIMERecord
from urlparse import urlparse

class App():
	def __init__(self):
		print("Pawn Shy application init...")
		self.hibp_lookup = HibpLookup()
		self.nfc_reader = NfcReader()
		self.card_id_lookup = CardIdLookup()
		self.led_driver = LedDriver()

	def start(self):
		print("Running Pawn Shy application. Press Ctrl-C to quit")

		self.led_driver.start()

		while True:
			try:
				uid, ndef_record = self.nfc_reader.poll_for_card()

				print ("Card reader poll result:")
				print uid
				print ndef_record

				if not ndef_record:
					self.do_card_id_lookup(uid)
				else:
					if isinstance(ndef_record, URIRecord): # - website. (if starts with http or https. Also check email:
						self.do_ndef_web_lookup(uid, ndef_record)
					elif isinstance(ndef_record, MIMERecord):
						self.do_ndef_email_lookup(uid, ndef_record)
					else:
						print("Don't know how to handle ndef record. reverting to card id.")
						self.do_card_id_lookup(uid)

				# Sleep for a bit to show the result then return to not busy led animation
				time.sleep(15)
				self.led_driver.animate_whilst_not_busy()
			except KeyboardInterrupt:
				self.nfc_reader.close()
				exit()
			except Exception as e:
				print("Error: " + e)
				# Ignore and continue....

	# Expect ndef to be MIMERecord
	# and the MIMERecord to be a vcard
	def do_ndef_email_lookup(self, uid, ndef_record):
		print("Email lookup. Mime type:")
		print (ndef_record.mimeType)
		print("Email lookup. Data:")
		print (ndef_record.data)

		self.do_email_lookup("Test@domain.com")

	def do_email_lookup(self, email):

		self.led_driver.animate_whilst_hibp_lookup()
		count, results = self.hibp_lookup.lookup_email(email)

		# Ignore the results for now but we might want to print them
		# for the person to take away.

		# Show the pwn count.
		self.led_driver.show_result_email_count(count)

	# Expect URIRecord
	def do_ndef_web_lookup(self, uid, ndef_record):
		print("Web address lookup")
		uri = ndef_record.uri
		print(uri)

		print("Extract domain")
		parsed_uri = urlparse(uri)
		domain = '{uri.netloc}'.format(uri=parsed_uri)
		# Bit of a hack to try and remove www and m. from domain names
		# as they cause HIBP to
		domain = domain.replace('www.', '')
		domain = domain.replace('m.', '')
		print ("'" + domain + "'")

		# Bodge warning!
		# TODO: If uri starts with "http://mobile.board.net" it's the Signal NFC
		# namebadge. Use card id lookup instead
		if domain == "mobile.bcard.net":
			return self.do_card_id_lookup(uid)

		self.do_web_lookup(domain)

	def do_web_lookup(self, domain):

		self.led_driver.animate_whilst_hibp_lookup()
		count, results = self.hibp_lookup.lookup_domain(domain)

		# Ignore the results for now but we might want to print them
		# for the person to take away.

		# Show the pwn count.
		self.led_driver.show_result_web_count(count)


	def do_card_id_lookup(self, card_id):
		print("Card id lookup")
		# Total hack...
		# Use card UID to lookup against a known database
		# for the email address.
		# Or for non-programmable cards, use the id for domain lookup.
		if card_id == "0430ACD2865880":
			print("Steves Signal card")
			self.do_email_lookup("Stephen.Harrison@AnalysisUK.com")
		elif card_id == "62EB23EE":
			print("Tesco.com blank rfid card")
			self.do_web_lookup("Tesco.com")
		elif card_id == "22D3530D":
			print("Badoo.com blank rfid card")
			self.do_web_lookup("Badoo.com")
		elif card_id == "74B44677":
			print("Biohack.me blank rfid card")
			self.do_web_lookup("Biohack.me")
		else:
			print("Unknown card")

# Main program logic follows:
if __name__ == '__main__':
	app = App()
	app.start()

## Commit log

2017-11-06 Adding case
    [Base.scad, Base.stl, LEDHolder.scad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]
2017-11-06 Minor update for nfc board notes.
2017-11-06 Moved nfc board test scrupt to testers folder.
2017-11-06 Adding neopixel drivers.
2017-11-06 Updated base to allow for the NFC reader now being on the left of the case (as the USB lead snagged when centered).
    [Base.scad, Base.stl]
2017-11-06 Added start of LED driver to show LED animations
2017-11-06 Corrected LED count for neopixel tester.
    [Neopixels.py]
2017-11-06 fleshed out a bit more of led modes.
2017-11-06 Added threading to run the animations on a background thread.
    Removed sleep between loops.
2017-11-06 fleshed out a little more of the application.
    updated LedDriver filename to be lowercase to start
2017-11-06 Tweaking results LED
2017-11-06 Set to show the result once only rather than repeadly on the loop.
    Fix bug for animate.
    [ledDriver.py]
2017-11-06 Implemented a few hacks for Twilio Signal card to prevent usage of the uri and a few other improvements.
    [app.py]
2017-11-06 improved domain lookup / led status.
2017-11-06 Added returning results to the Have I Been Pwned lookup so these can be printed or something done with them.
    Implemented domain lookup from HIBP
2017-11-06 fix for string/int contat not allowed by python
    [hibpLookup.py]
2017-11-06 fixed query string formatting issue
    [hibpLookup.py]
2017-11-06 Added replacement of www. and m. from domain as these don't work well with HIBP and are common on uri's sent via p2p nfc from phone.
    Added un-programmable card id lookups for Badoo and Biohack
    [app.py]
2017-11-06 Added exception handler for keyboard exception (i.e. Ctrl+C) to close the NFC reader.
    Added general exception handler to ignore errors and carry on.
    [app.py, nfcReader.py]
2017-11-06 Added links for nfc sensor and leds
